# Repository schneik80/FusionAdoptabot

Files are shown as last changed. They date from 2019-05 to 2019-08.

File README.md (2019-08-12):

# FusionAdoptabot
  
This is an adaptation of Printrbot's Adoptabot original design (https://www.brookdrumm.com/3dprinters1).  
  
This Adaptation, removes Printerbot proprietary parts.  
* Hotend is replaced with E3D V6 All metal hotend  
* Extruder is an E3D Titan  
* The bed sensor is a BLtouch  
* Electronics are Arduino Mega + Ramps 1.4-1.6  
  
PLA Parts all printed with 3 or 4 Permitars and 33% infill.  
Suports are not included as these will vary with your own printerbot.  
  
The only custom component is the Print bed.  
  
All credit goes to Brook for releasing this design into the community. Without his work this would not have been possible.  
  
**This design is licensed cc sharealike non comercial.**  
  
### 3D Models:  
The 3D design is included  as a Fusion F3Z. Download this Fusion Archive. Launch Fusion 360. Create a new Project and in the data pane click upload. Select the F3Z.
Fusion will unpack the archive and upload all the necissary parts and assemblies into the new project.  
  
The model is also provided as STEP203 and can be imported into most any 3D CAD tool.
  
### STL Files:  
Over the comming weeks I will extract and post the STL files. You can get these yourself from the above 3D models.    
Posting of the STL files is only a convience for those looking to simply print and assemly the printer.  
  
### Firmware:
A work in progress firmware is available here: https://github.com/schneik80/Marlin-FusionAdoptabot  
The firmware currenly support kinimatic setings only. Hotend configuration is TBD.  

### Images:

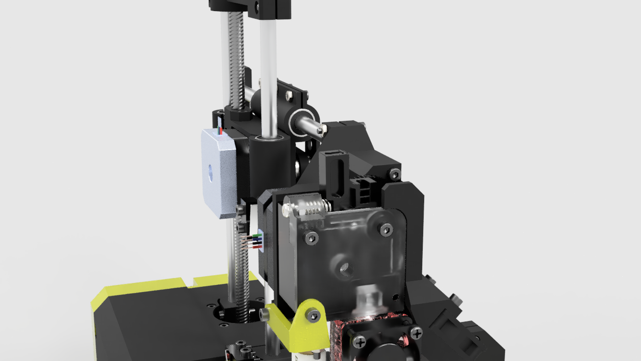
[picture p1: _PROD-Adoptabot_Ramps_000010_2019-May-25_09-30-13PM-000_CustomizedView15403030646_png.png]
  
  
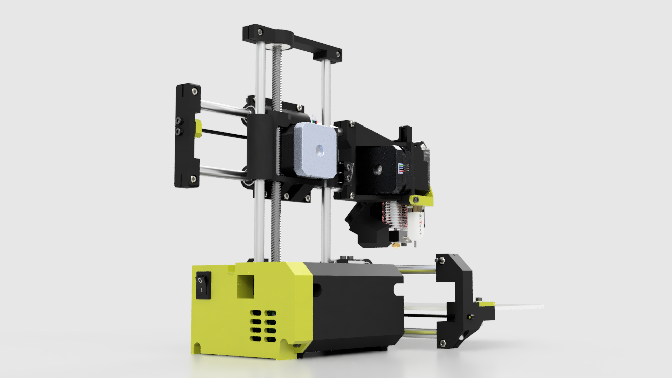
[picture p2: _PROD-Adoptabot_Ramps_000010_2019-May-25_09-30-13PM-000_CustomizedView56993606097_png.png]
  
  
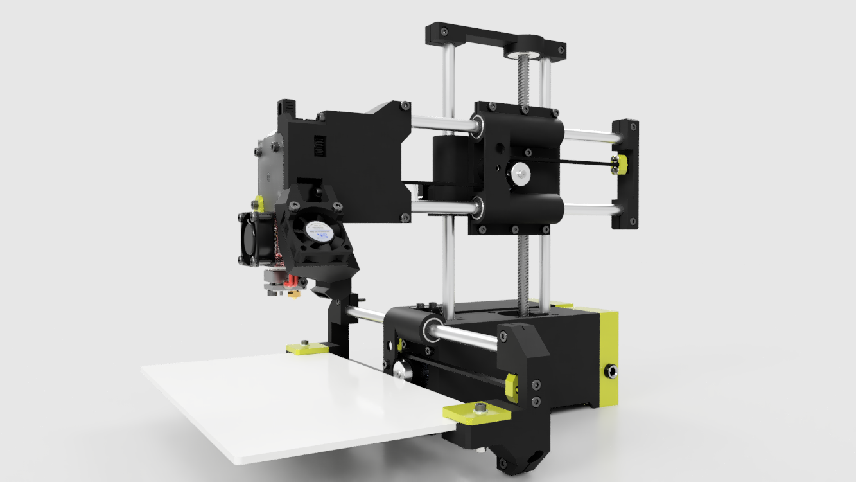
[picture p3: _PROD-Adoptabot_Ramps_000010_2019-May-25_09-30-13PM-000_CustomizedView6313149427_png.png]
  
  
### Bill of Materials PROD-Adoptabot Ramps 000010 v26:     

**X Bar End Clamp Right**|**PLA**|**1**
:-----:|:-----:|:-----:
X Build Plate Clamp Right v1|PLA|1
Belt Tensioner|PLA|1
X Bearing Block|PLA|1
Z Bearing Block|PLA|1
TR8 Nut|PLA|1
Z Bar Clamp|PLA|1
Extruder Mount|PLA|1
Cooling Fan Shroud|PLA|1
Cooling Fan Shroud Mount|PLA|1
BLTouch Bracket|PLA|1
Y Bar End Clamp|PLA|1
Belt Tensioner|PLA|1
Y Bearing Block|PLA|1
Ramps Cover|PLA|1
ISO 4762 - M3 X 8|Steel, Alloy|13
ISO 4762 - M3 X 10|Steel, Alloy|5
ISO 4762 - M3 X 12|Steel, Alloy|13
ISO 4762 - M3 X 16|Steel, Alloy|6
ISO 4762 - M3 X 20|Steel, Alloy|15
ISO 4762 - M3 X 35|Steel, Alloy|3
ISO 4032 - M3|Steel, Alloy|25
Locknut M3|Steel, Alloy|2
ISO 7089 - 3 - 140 HV(1)|Steel, Alloy|4
ISO10642-M3x8|Steel, Alloy|4
RAMPS1\_4| |1
Limit Switch - 10T85| |2
E3D v6 HotEnd| |1
BL-touch| |1
Titan Extruder| |1
Rocker Switch 10A|Steel|1
DC Jack 5.5 X 2.1mm| |1
NEMA-17 Stepper Motor + TR8 X 210mm Leadscrew| |1
NEMA 17 Stepper Motor - 34mm| |2
NEMA 17 Stepper Motor - 23mm| |1
Fan 30 X 30 X 10 - 12v| |1

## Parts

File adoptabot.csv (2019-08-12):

Display Name | Part Number | Material | Count
GT2 20T Pully |  | Aluminum 6061 | 2 | x
GT2 Belt 350mm | 217-00010 | Rubber, Black | 2 | x
.125 Print Plate | 124-00005 | Aluminum 6061 | 1 | x
8 x 225mm Bar | 217-00008 | Aluminum 6061 | 2 | x
8 x 200mm Bar | 217-00008 | Aluminum 6061 | 4 | x
624 2Z - 13 x 4 x 5mm Bearing | 159-00004 | Steel | 4 | x
608 2Z 8 x 22 x 7mm Bearing | 159-00005 | Steel | 1 | x
LM8UU | 159-00003 | Steel | 12 | x
Case Rear | 098-00003 | PLA | 1
Side Case Plate |  | PLA | 1
Main Housing | 098-00002 | PLA | 1
Z Motor Shim | 098-00004 | PLA | 1
X Bar End Clamp Left | 098-00006 | PLA | 1
X Build Plate Clamp Left | 098-00007 | PLA | 1
X Bar End Clamp Right | 098-00008 | PLA | 1
X Build Plate Clamp Right v1 | 098-00009 | PLA | 1
Belt Tensioner | 098-00010 | PLA | 1
X Bearing Block | 098-00015 | PLA | 1
Z Bearing Block | 098-00018 | PLA | 1
TR8 Nut | 098-00019 | PLA | 1
Z Bar Clamp | 098-00017 | PLA | 1
Extruder Mount | 098-00011 | PLA | 1
Cooling Fan Shroud |  | PLA | 1
Cooling Fan Shroud Mount | 098-00013 | PLA | 1
BLTouch Bracket | 098-00012 | PLA | 1
Y Bar End Clamp | 098-00014 | PLA | 1
Belt Tensioner | 098-00010 | PLA | 1
Y Bearing Block | 098-00016 | PLA | 1
Ramps Cover | 098-00005 | PLA | 1
ISO 4762 - M3 X 8 | 156-00007 | Steel, Alloy | 13
ISO 4762 - M3 X 10 | 156-00008 | Steel, Alloy | 5
ISO 4762 - M3 X 12 | 156-00009 | Steel, Alloy | 13
ISO 4762 - M3 X 16 | 156-00010 | Steel, Alloy | 6
ISO 4762 - M3 X 20 | 156-00011 | Steel, Alloy | 15
ISO 4762 - M3 X 35 | 156-00012 | Steel, Alloy | 3
ISO 4032 - M3 | 153-00003 | Steel, Alloy | 25
Locknut M3 | 153-00002 | Steel, Alloy | 2
ISO 7089 - 3 - 140 HV(1) | 157-00005 | Steel, Alloy | 4
ISO10642-M3x8 | 156-00006 | Steel, Alloy | 4
RAMPS1_4 | RAMPS1_4 |  | 1
Limit Switch - 10T85 | 217-00002 |  | 2 | x
E3D v6 HotEnd | E3D v6 HotEnd - Heatsink |  | 1 | x
BL-touch | 699-00007 |  | 1 | x
Titan Extruder |  |  | 1 | x
Rocker Switch 10A | 217-00003 | Steel | 1 | x
DC Jack 5.5 X 2.1mm | 217-00004 |  | 1 | x
NEMA-17 Stepper Motor + TR8 X 210mm Leadscrew |  |  | 1 | x
NEMA 17 Stepper Motor - 34mm | 301-00004 |  | 2 | x
NEMA 17 Stepper Motor - 23mm | 301-00005 |  | 1 | x
Fan 30 X 30 X 10 - 12v | 380-00001 |  | 1

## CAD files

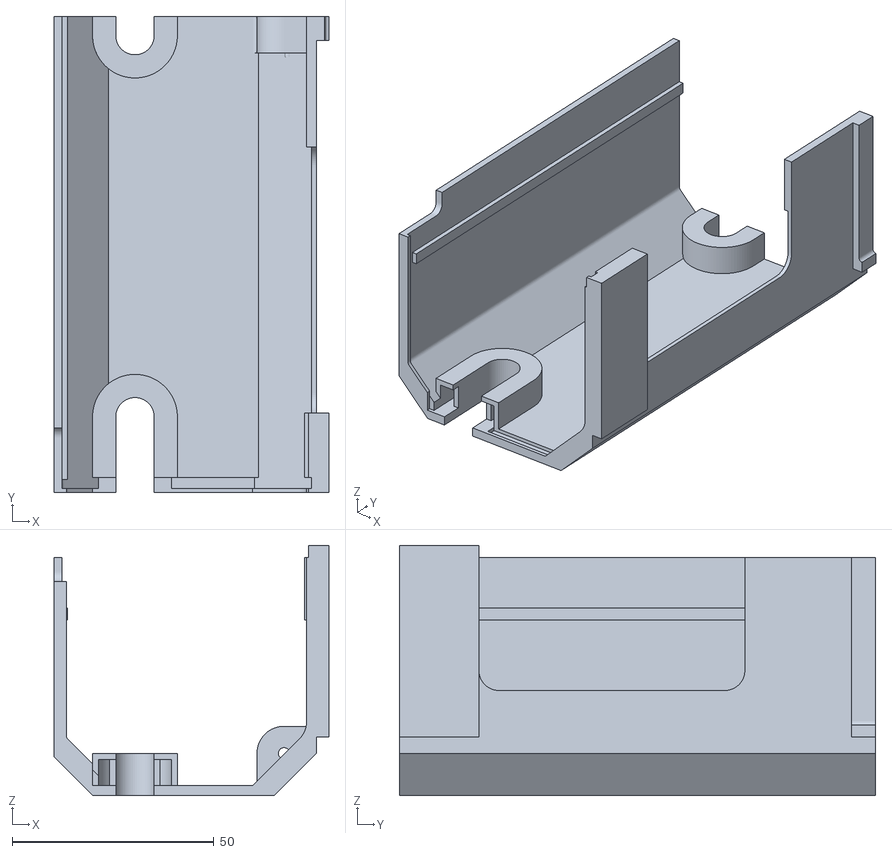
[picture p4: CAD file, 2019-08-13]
Stl Files/Print Bed 2 v3.stl
68.0 x 117.9 x 62.0

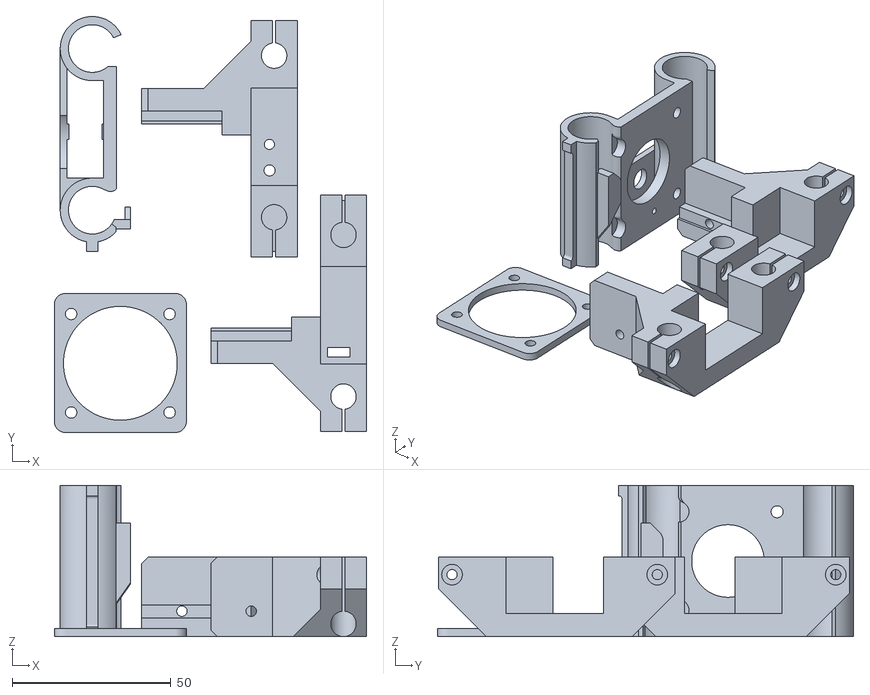
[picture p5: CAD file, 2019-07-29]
Stl Files/Print Bed 3 v3.stl
98.4 x 131.0 x 47.6

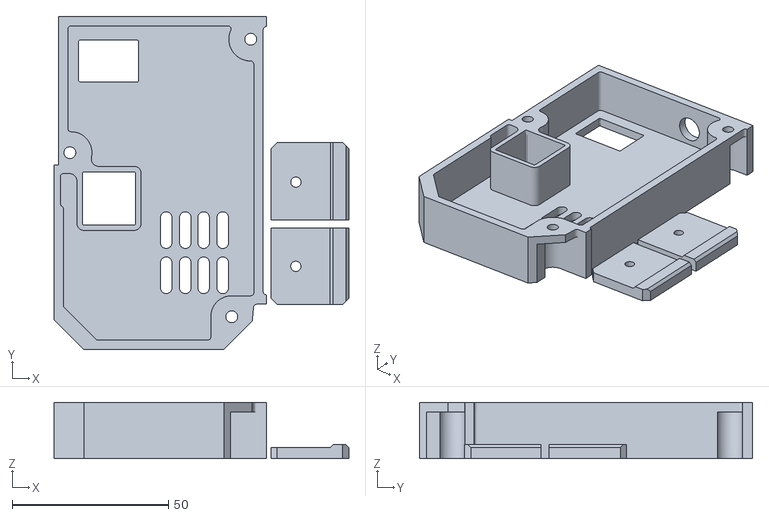
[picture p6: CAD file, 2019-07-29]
Stl Files/Print Bed Alt Color 1 v2.stl
94.5 x 106.6 x 18.0

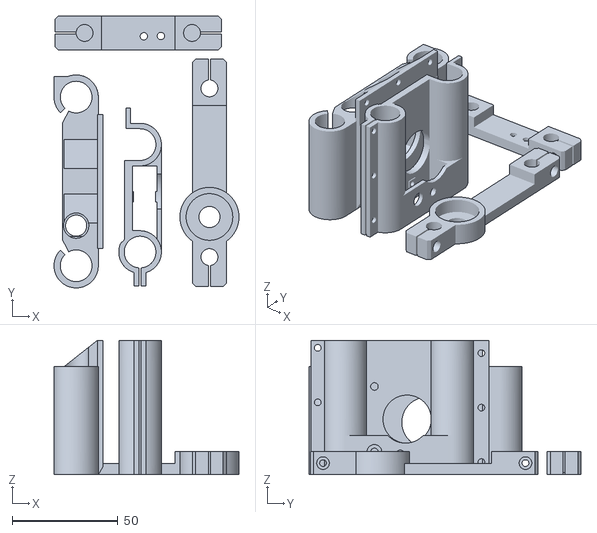
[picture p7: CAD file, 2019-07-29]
Stl Files/Print Bed 4 v2.stl
87.6 x 128.8 x 63.7

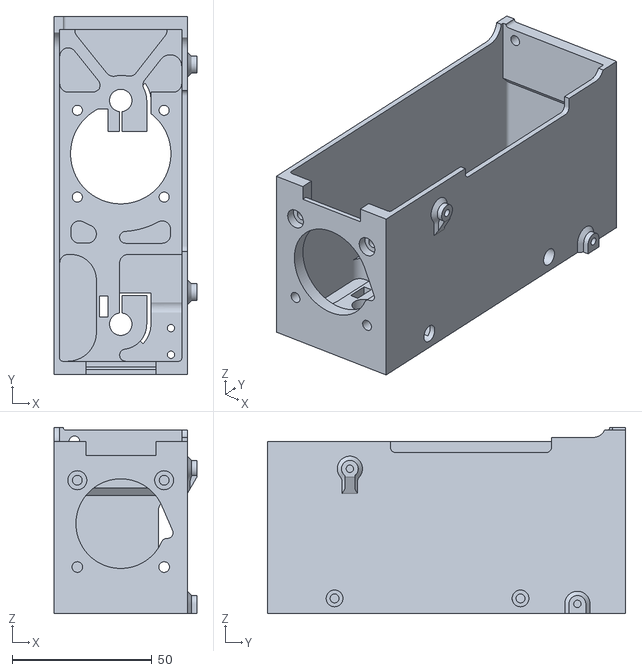
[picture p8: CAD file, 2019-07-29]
Stl Files/Print Bed 1 v2.stl
51.0 x 127.9 x 66.5

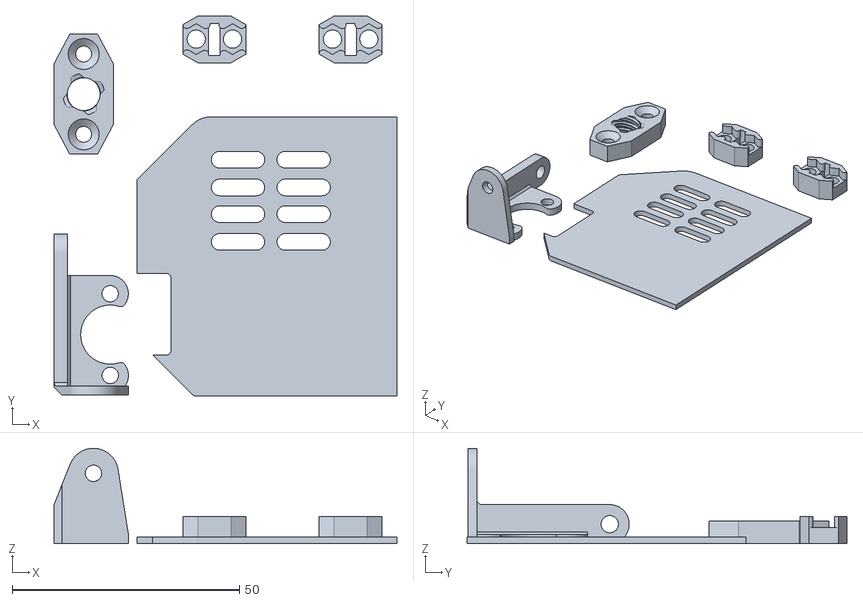
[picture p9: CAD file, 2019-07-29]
Stl Files/Print Bed Alt Color 2 v3.stl
75.5 x 83.7 x 21.0

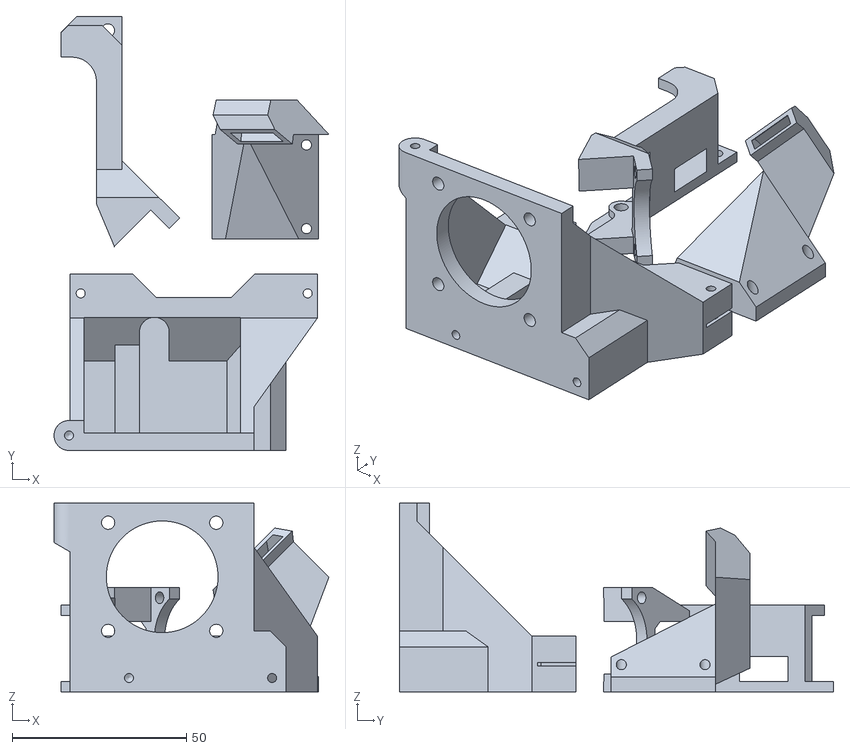
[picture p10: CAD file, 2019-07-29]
Stl Files/Print Bed 5 v2.stl
78.8 x 124.4 x 54.2

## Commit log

2019-05-25 Create BOM
2019-07-29 Print Sets for R1
    [Print Bed 1 v2.stl, Print Bed 2 v2.stl, Print Bed 3 v3.stl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]
2019-08-12 BOM Updates
2019-08-12 CSV BOM Changes
    [adoptabot.csv]
2019-08-13 BED 1 upload
    [Print Bed 1 v2.stl]
2019-08-13 Bed 2 updates
    [Print Bed 2 v3.stl]
